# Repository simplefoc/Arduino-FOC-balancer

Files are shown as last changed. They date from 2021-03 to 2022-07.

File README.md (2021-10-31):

# Arduino *Simple**FOC**Balancer*

Modular Arduino two wheel balancing robot based on gimbal BLDC motors and *Simple**FOC**library*.
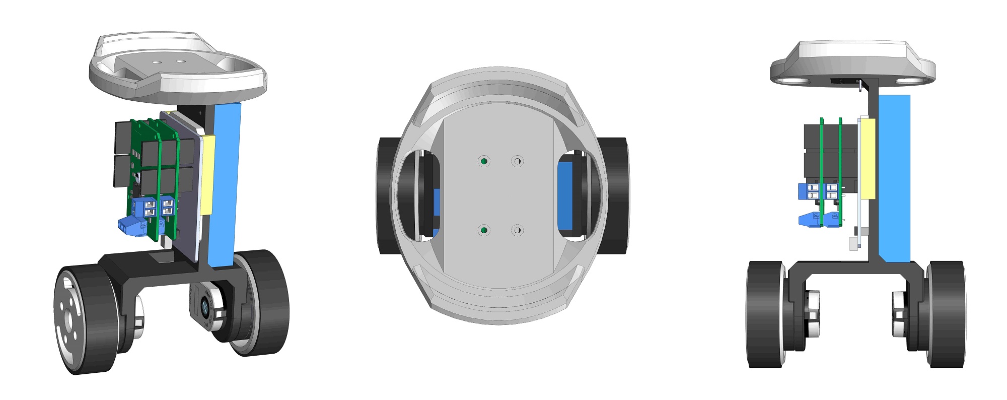
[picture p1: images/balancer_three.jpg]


Balancing robots are always a bit tricky to design, in order to make the robot balance we need to design and tune our mechanical structure and the control algorithm and, in the same time, choose optimal motors, sensors and microcontrollers. Therefore, even though BLDC motors are a great choice for balancing robots the complexity of their control made them undesirable. So this robot is an attempt to create a simple and modular, BLDC motor based, balancing robot that can be easily adapted for different *motor+sensor+mcu+driver* combinations and to show off the power and the awesome dynamics of gimbal BLDC motors 😄

## YouTube video demo
<a href="https://www.youtube.com/watch?v=f9GJqqUpL2w">
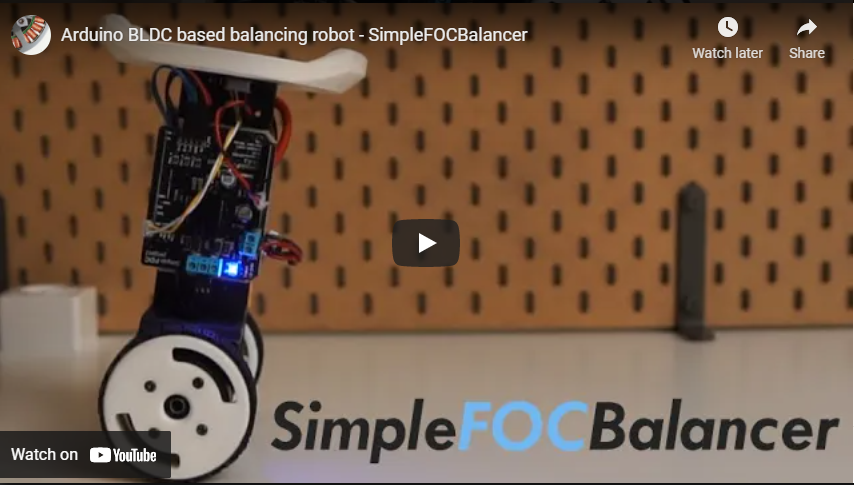
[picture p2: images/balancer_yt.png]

</a>

## Readme structure
- [Mechanical components](#mechanical-components)
    - [ 3D printed parts](#3d-printed-parts)
    - [Hardware parts](#hardware-parts)
- [Electrical components](#electrical-components)
    - [BLDC motor](#bldc-motor)
    - [Position sensors](#position-sensors)
    - [BLDC motor](#bldc-driver)
    - [IMU module](#imu-module)
    - [Bluetooth module](#bluetooth-module)
    - [Microcontroller](#microcontroller)
- [Arduino Code](#arduino-code)
    - [Control algorithm](#control-algorithm)
    - [Bluetooth remote control](#bluetooth-remote-control)

## Mechanical components
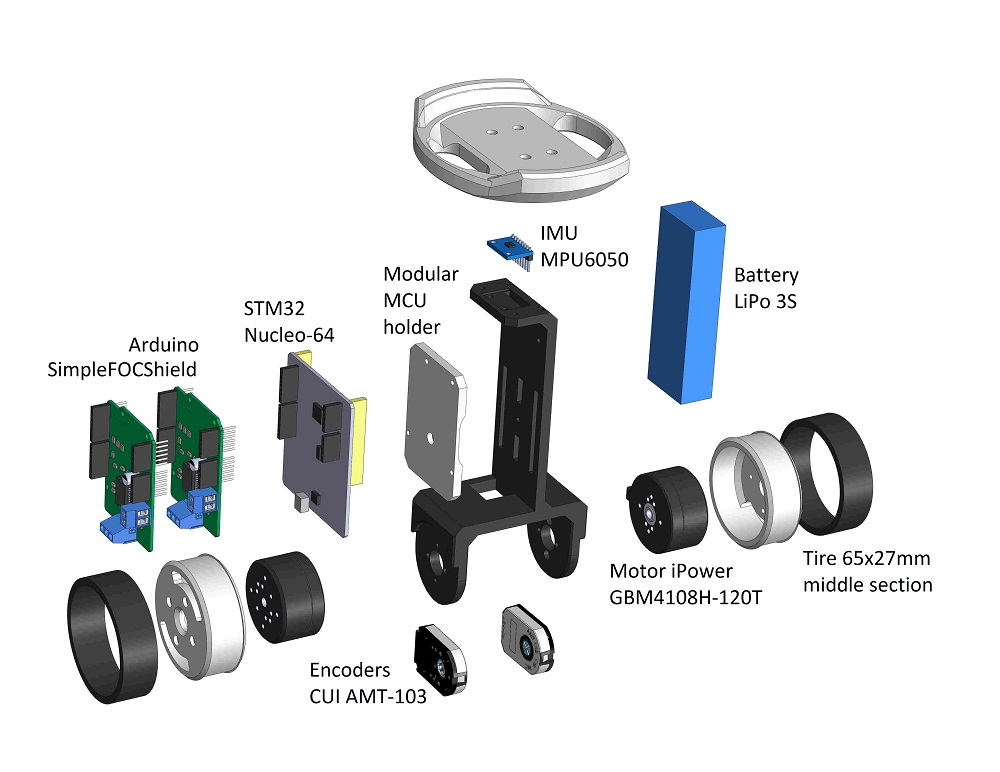
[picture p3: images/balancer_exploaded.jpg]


### 3D printed parts
This balancer project has 5 3d printed parts. You can find them in the `CAD > STL` directory. They are:
- center frame (`FOC_balancer.stl`)
    - infill: `30%`
    - layer hight: `>0.15mm`
- wheels (`wheel.stl`) 
    - infill: `30%`
    - layer hight: `0.1-0.15mm`
    - ***reasonably precise***
- MCU mount (`arduino_holder.stl`)
    - infill: `30%`
    - layer hight: `>0.15mm`
- top plate (`top_plate.stl`)
    - infill: `20%`
    - layer hight: `>0.15mm`

I have printed the pendulum in the PLA filament but there should be no real difference in using PETG or ABS filaments, this is just what I had in hand at the moment.

You will also find all the CAD files used in this project in the `CAD` folder. I have included the Solidworks 2016 parts and the full assembly. Additionally all the parts are exported to STEP format for easier porting to the other CAD IDEs.

> Beware: 
I have designed the holes on the pendulum arm and the wheel to match perfectly the motor the encoders I was using, so please check the dimensions of your motors and encoder holes before printing 😄
***If you would prefer some other CAD format, let me know, maybe I can export it differently.***

### Hardware parts

The mechanical components you will need are two sets of screws which you can easily find in your hardware store and the RC car tires that can be bought in bulk online. 

Component | Description | Link | Price
---- | ---- | ---- | ----
 |M3 screws<br> 25pcs <br> M3x10mm | [Ebay](https://www.ebay.com/itm/M2-M2-5-M3-M4-M5-M6-M8-Stainless-Steel-Metric-Hex-Socket-Head-Cap-Screws-Bolt/123439613021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) | 2$
 | M4 screws & nuts<br> 2pcs <br> M4x50mm | [Ebay](https://www.ebay.com/itm/M2-M2-5-M3-M4-M5-M6-M8-Stainless-Steel-Metric-Hex-Socket-Head-Cap-Screws-Bolt/123439613021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) | 4$
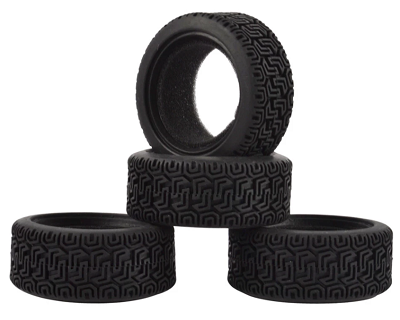
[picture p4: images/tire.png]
 |RC wheel <br>HSP HPI 8014 <br>2pcs <br> 69.5mmx29mm | [Aliexpress](https://www.aliexpress.com/item/32947563689.html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,searchweb201602_,searchweb201603_) | 5$

## Electrical components
### BLDC motor
The BLDC motors I was using in my video are an old versions of the [iPower GM4108](https://shop.iflight-rc.com/index.php?route=product/product&product_id=217&search=GM4108H-120T) motors which are not available anymore, in any case I was not able to find a website that would sell them. 
The good news is that you can use basically any other gimbal motor in that class with only minor modifications, mostly in the CAD parts - change the mounting holes positions. Some of the motors I was able to find that would be the most similar to my motor would be:

Component | Description | Link | Price
---- | ---- | ---- | ----
 | iPower Motor GM4108H-120T | [iFlight webshop](https://shop.iflight-rc.com/index.php?route=product/product&product_id=217&search=GM4108H-120T) | 35$
 | BGM4108-150HS | [Ebay](https://www.ebay.com/itm/New-Brushless-Gimbal-Motor-BGM4108-150HS-24N22P-for-Sony-NEX5-7-Camera-Mount-DIY/261903969970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) | 32$

### Position sensors
In my case I was using two encoders for the two motors. Now, this is very specific to my particular implementation, with minor CAD modifications you can use any type of the position sensor that is supported by the *Simple**FOC**library*. [Click here](https://docs.simplefoc.com/position_sensors) to see the documentation of the supported sensors. 

The encoders I have used in this project are:

 | AMT103 CUI | [Mouser](https://eu.mouser.com/ProductDetail/CUI-Devices/AMT103-V?qs=WyjlAZoYn51X2GCrrvGQTg==T) | 20$
---- | ---- | ---- | ----

### BLDC driver
In this project I used the [*Simple**FOC**Shield* v2.0.3](https://docs.simplefoc.com/arduino_simplefoc_shield_showcase) which is basically an Arduino shield which enables the usage of the FOC algorithm with the BLDC motors. It is practically plug & play in combination with the Arduino [*Simple**FOC**library*](https://docs.simplefoc.com/arduino_simplefoc_library_showcase).

But there is a lot of different boards that you can use to make this balancer. Basically any gimbal motor driver that is supported by the *Simple**FOC**library* will be suitable.  [Click here](https://docs.simplefoc.com/bldc_drivers) to see the documentation of the supported drivers. Here are some examples of the possible BLDC drives you could use:

Examples | Description | Link | Price
---- | ---- | ---- | ---
[](https://simplefoc.github.io/simplefoc_shield_product)| *Simple**FOC**Shield* v1/v2 | [More info](https://simplefoc.github.io/simplefoc_shield_product) | 20$
[](https://www.ebay.com/itm/BGC-3-1-MOS-Large-Current-Two-Axis-Brushless-Gimbal-Controller-Driver-Alexmos/302692769869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)| BGC 3.1 | [More info](https://www.ebay.com/itm/BGC-3-1-MOS-Large-Current-Two-Axis-Brushless-Gimbal-Controller-Driver-Alexmos/302692769869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) | 10$
[](https://www.ebay.com/itm/Storm32-BGC-32Bit-3-Axis-Brushless-Gimbal-Controller-V1-32-DRV8313-Motor-Driver/174343022855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) | Storm32 BGC | [Ebay](https://www.ebay.com/itm/Storm32-BGC-32Bit-3-Axis-Brushless-Gimbal-Controller-V1-32-DRV8313-Motor-Driver/174343022855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) | 25$

## IMU module

I've used the IMU MPU6050 with integrated DMP. It is a great board, very cheap and very powerful. You can use any other accelerometer to make the balancing robot but you might need to do some coda adaptation, mostly in the `imu_helpers.cpp/h`.

Examples | Description | Link | Price
---- | ---- | ---- | ---
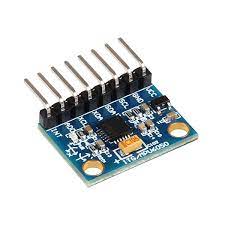
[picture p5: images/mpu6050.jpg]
[](https://www.amazon.fr/ARCELI-MPU6050-Acc%C3%A9l%C3%A9rom%C3%A8tre-Gyroscope-Convertisseur/dp/B07BVXN2GP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)| MPU6050  | [Amazon](https://www.amazon.fr/ARCELI-MPU6050-Acc%C3%A9l%C3%A9rom%C3%A8tre-Gyroscope-Convertisseur/dp/B07BVXN2GP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) | 2-5$

## Bluetooth module

If using the `ESP32` based mcu you will not need an additional Bluetooth module. But if you decide to go with some other mcu, I advise you to use the `HC-05`/`HC-06` modules, they are very simple to use and will work out of the box with the code.

Examples | Description | Link | Price
---- | ---- | ---- | ---
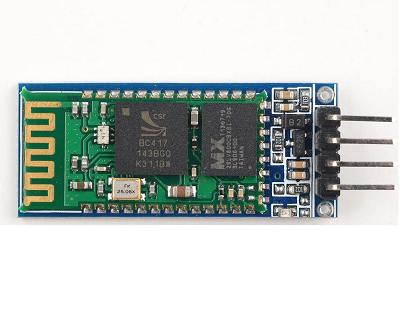
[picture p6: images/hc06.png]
[](https://www.amazon.fr/SunFounder-Wireless-Bluetooth-Transceiver-Backplane/dp/B00GAXG9A6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)| HC-06  | [Amazon](https://www.amazon.fr/SunFounder-Wireless-Bluetooth-Transceiver-Backplane/dp/B00GAXG9A6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) | 2-10$

## Microcontroller

In my example I've used EPS32 based microcontroller and the Stm32 based one but any type of the MCU that is supported by the *Simple**FOC**library* will do. [Click here](https://docs.simplefoc.com/microcontrollers) to see the documentation of the supported microcontrollers. 

Examples | Description | Link | Price
---- | ---- | ---- | ---
[](https://simplefoc.github.io/simplefoc_shield_product)| WeMos D1 R32  | [More info](https://www.amazon.com/Arduino-Wireless-Bluetooth-Development-Memory/dp/B07W1K56LN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) | 10$
[](https://www.mouser.fr/ProductDetail/STMicroelectronics/NUCLEO-F446RE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)| Nucleo-64 F411RE | [More info](https://www.mouser.fr/ProductDetail/STMicroelectronics/NUCLEO-F446RE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) | 15$

If using the gimbal controller boards such as BGC3.0/BGC3.1, Storm32 or similar you will do not bea able to change your microcontroller because it is integrated into the boards.

## Arduino code

still not complete

### Control algorithm
The control algorithm implemented in the Arduino sketch is very simple. It is a 2 PID controller cascade shown on the image bellow. 

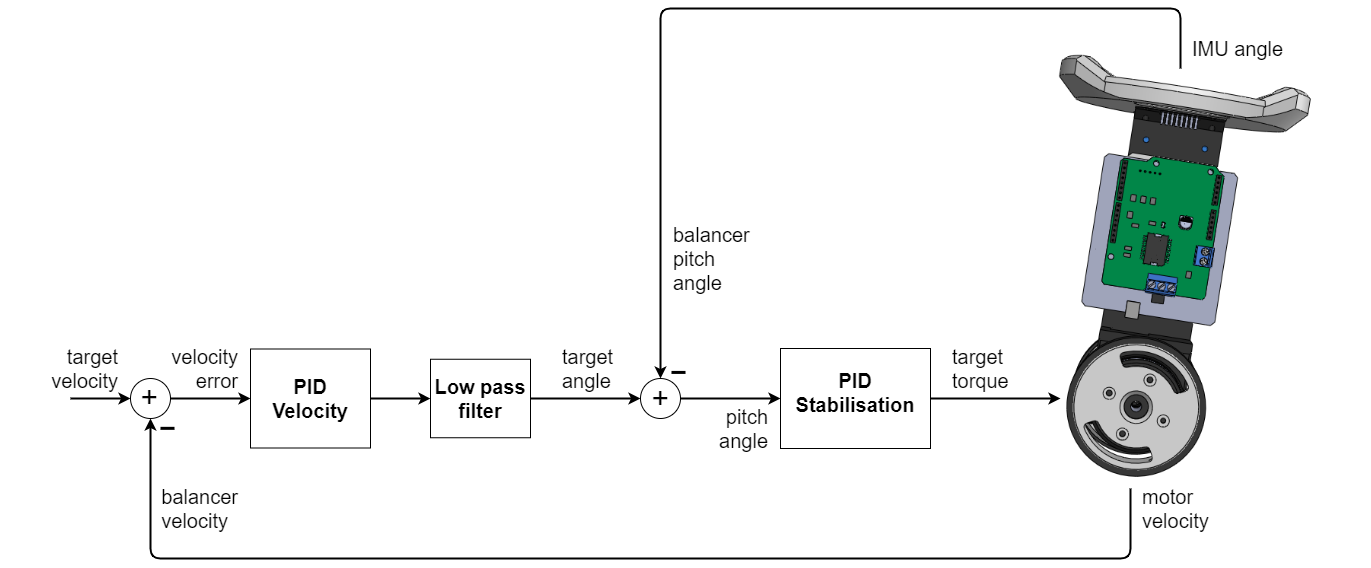
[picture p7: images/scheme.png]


The PID stabilisation controller will make sure that any target angle that is defined by the PID velocity is reached as soon as possible. Where PID velocity will try to keep the balancer robot moving with desired velocity defined by the user. This simple scheme is very powerful because it will make the balancer stand still even if the balancer zero angle has some offset. 

Here is the arduino code of the controller:
```cpp
// read pitch from the IMU
float pitch = getPitchIMU();
// calculate the target angle for throttle control
float target_pitch = lpf_pitch_cmd(pid_vel((motor1.shaft_velocity + motor2.shaft_velocity) / 2 - lpf_throttle(throttle)));
// calculate the target voltage
float voltage_control = pid_stb(target_pitch - pitch);

// filter steering
float steering_adj = lpf_steering(steering);
// set the tergat voltage value
motor1.target = voltage_control + steering_adj;
motor2.target = voltage_control - steering_adj;
```
The balancer velocity is estimated as average velocity for each wheel separately `(motor1.shaft_velocity + motor2.shaft_velocity) / 2`.  The target velocity is defined by the `throttle` variable set by the user. In addition to the `throttle` user can set the `steering` variable which will determine turning rate of the robot. The units of the `steering` variable are Volts in the provided example.

The PID parameters and filtering values can be changed by changing the definition of the `pid_stb` and `pid_vel`:
```cpp
// control algorithm parameters
// stabilisation pid
PIDController pid_stb{.P = 30, .I = 100, .D = 1, .ramp = 100000, .limit = 7};
// velocity pid
PIDController pid_vel{.P = 0.01, .I = 0.03, .D = 0, .ramp = 10000, .limit = _PI / 10};
// velocity control filtering
LowPassFilter lpf_pitch_cmd{.Tf = 0.07};
// low pass filters for user commands - throttle and steering
LowPassFilter lpf_throttle{.Tf = 0.5};
LowPassFilter lpf_steering{.Tf = 0.1};
```

### Bluetooth remote control

For remote controlling your robot you can use any wireless communication you wish. In my case I've used bluetooth with mobile joystick app. There is really a lot of them and you can choose the one that you prefer. In my case I've used an app called Gibalo. [Link to the google play app](https://play.google.com/store/apps/details?id=hr.fer.android.as46486.gibalo&hl=en&gl=US)

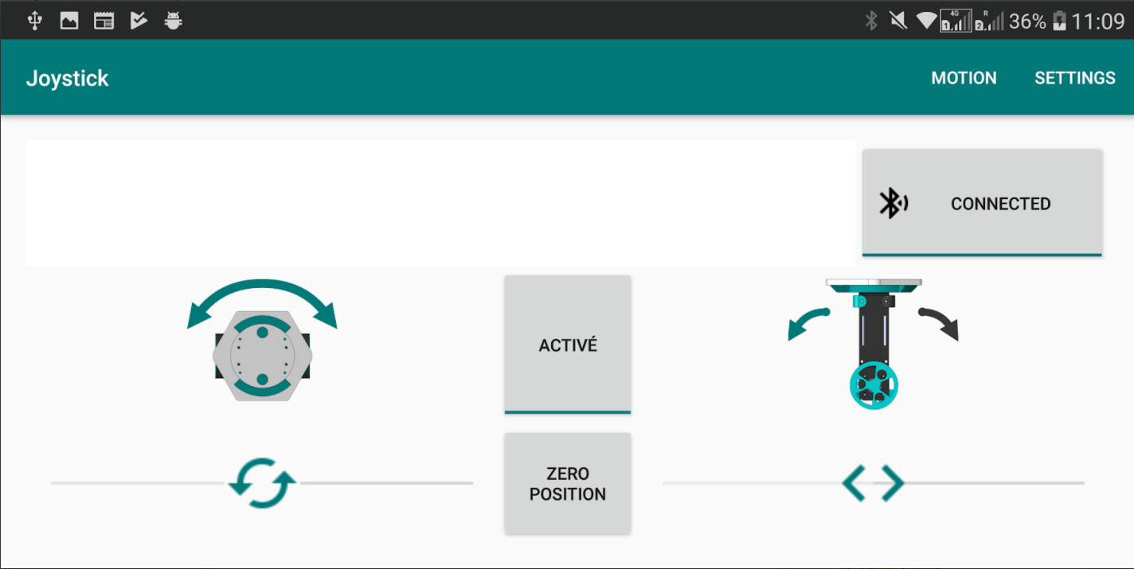
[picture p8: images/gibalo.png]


Regardless of the communication protocol that you choose to use the only three variables that you need to change in the balancer code are 
- `throttle` - target velocity of the balancer: value [-`max_throttle`, `max_throttle`] 
- `steering` - turning rate command: value [-`max_steering`, `max_steering`]
- `state` - `1` on,  `0` off

For the Gibalo app the Arduino code will be:
```cpp
/**
  Function intended for connecting to the Gibalo application
  In one byte it receives either throttle or steering command
  - if received byte  in range [0,200] then throttle command in between [-100, 100]
  - if received byte  in range [210,250] then steering command in between [-20, 20]
*/
void handleBluetooth(Stream& bt_port) {
  int inByte;
  if (bt_port.available() > 0) {
    while (bt_port.available()) {
      inByte = bt_port.read();
    }
    inByte = inByte - 100;
    if (inByte == 155) {
      // ON Byte
      steering = 0;
      throttle = 0;
      state = 1;
      bt_port.println("State ON");
    } else if (inByte == 154) {
      // OFF Byte
      steering = 0;
      throttle = 0;
      state = 0;
      bt_port.println("State OFF");
    } else if (inByte >= -100 && inByte <= 100) {
      // throttle set-point Byte
      throttle = max_throttle *  ((float)inByte) / 100.0;
    } else if (inByte >= 110 && inByte <= 150) {
      // steering set-point Byte
      steering = max_steering * ((float)(inByte - 130.0)) / 20.0;
    } else {
      // Error Byte
      steering = 0;
      throttle = 0;
      bt_port.println("Error number!");
    }
    bt_port.flush();
  }
}
```

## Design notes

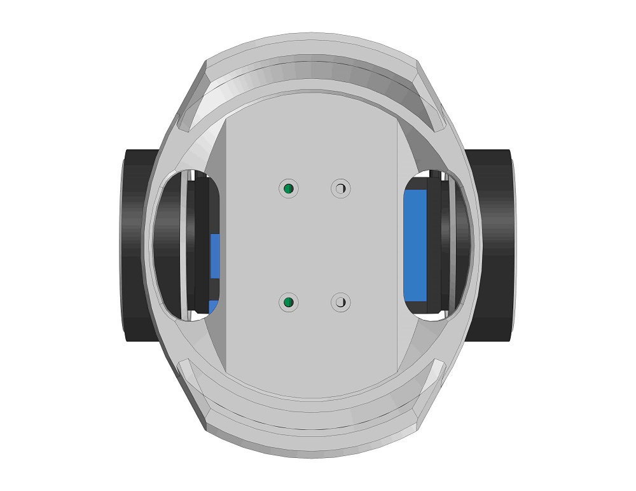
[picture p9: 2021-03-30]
images/balancer_t.JPG

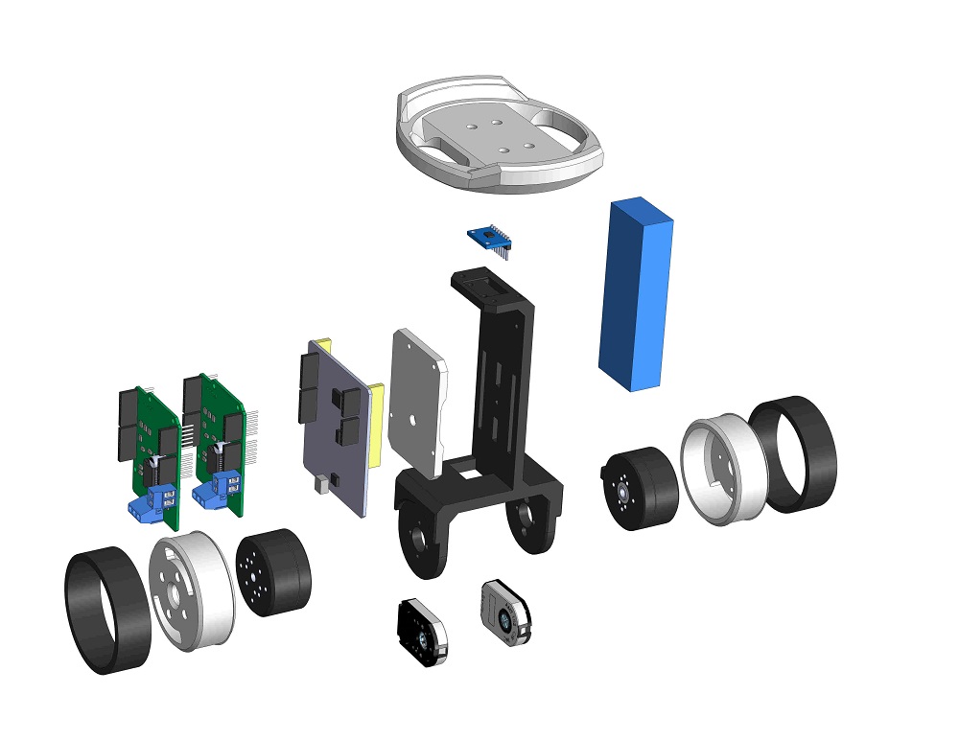
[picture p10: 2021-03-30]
images/balancer.JPG

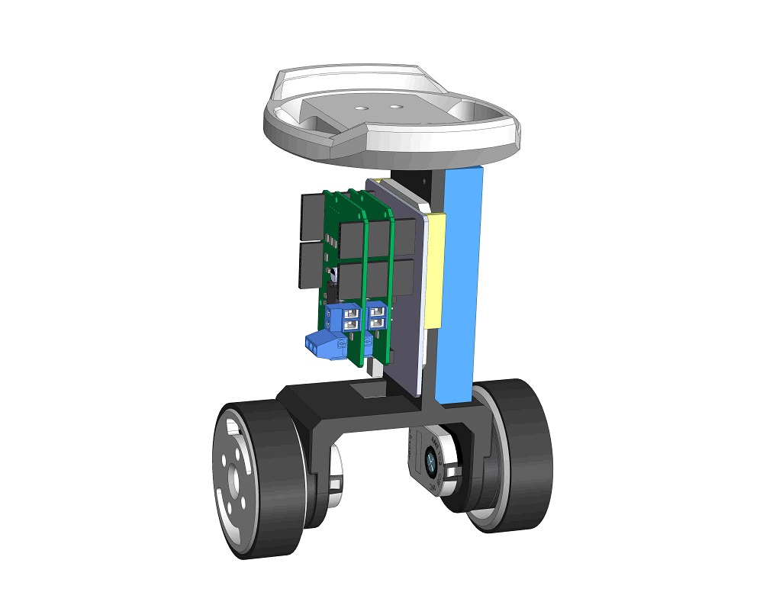
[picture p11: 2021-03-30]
images/balancer_s.JPG

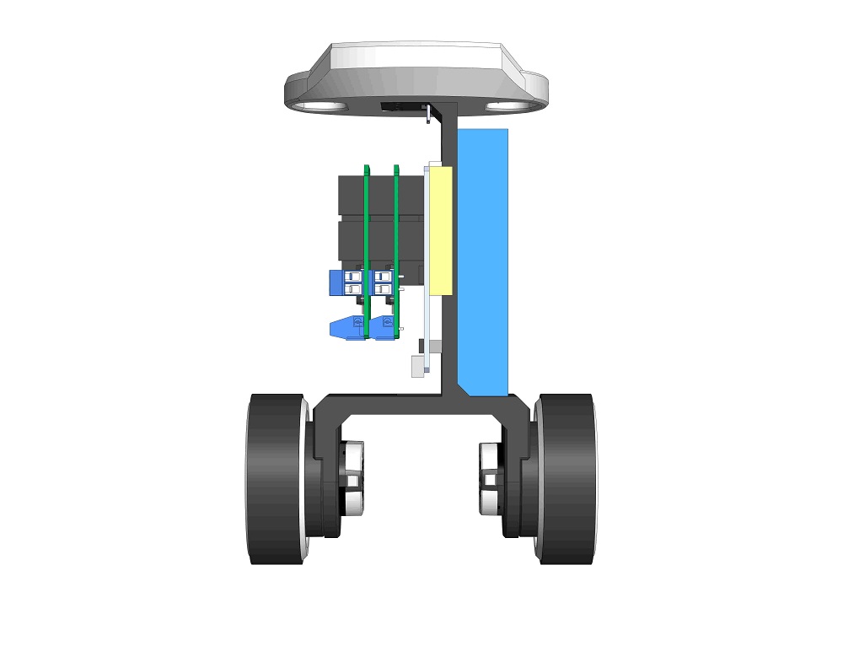
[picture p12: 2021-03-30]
images/balancer_front.JPG

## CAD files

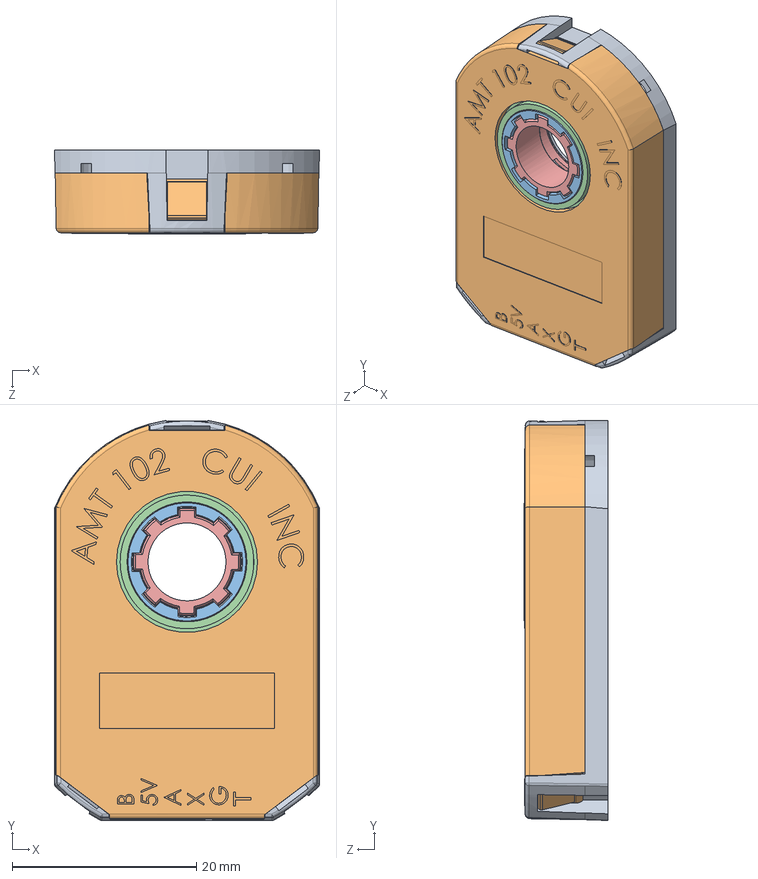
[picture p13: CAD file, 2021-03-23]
CAD/SolidWorks/AMT102/CUI_cui_amt102-0048-n2000-s.sldasm
28.8 x 43.4 x 9.15 mm
CUI_amt-102-base-rev-k
CUI_amt-102-top-cover-rev-h
CUI_amt-hub-top-rev-d1
CUI_amt-hub-bottom-rev-b
CUI_amt10x-shaft-adaptor-rev-e

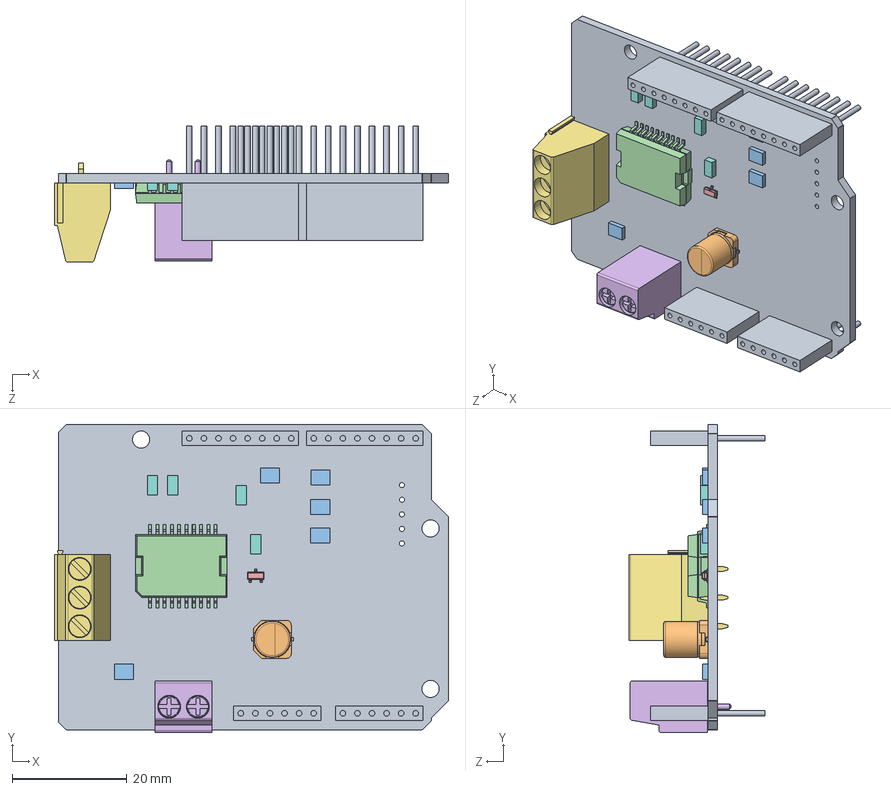
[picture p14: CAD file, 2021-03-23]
CAD/SolidWorks/SimpleFOCShield/ArduinoFOC.SLDASM
68.7 x 53.7 x 23.8 mm
Board
User_Library-A3D-003-00012
Extruded x 5
L6234PD x 2
User_Library-BAT54 x 2
2_RGB15238730
37753_RGB15238730
Extruded_2 x 4
headers

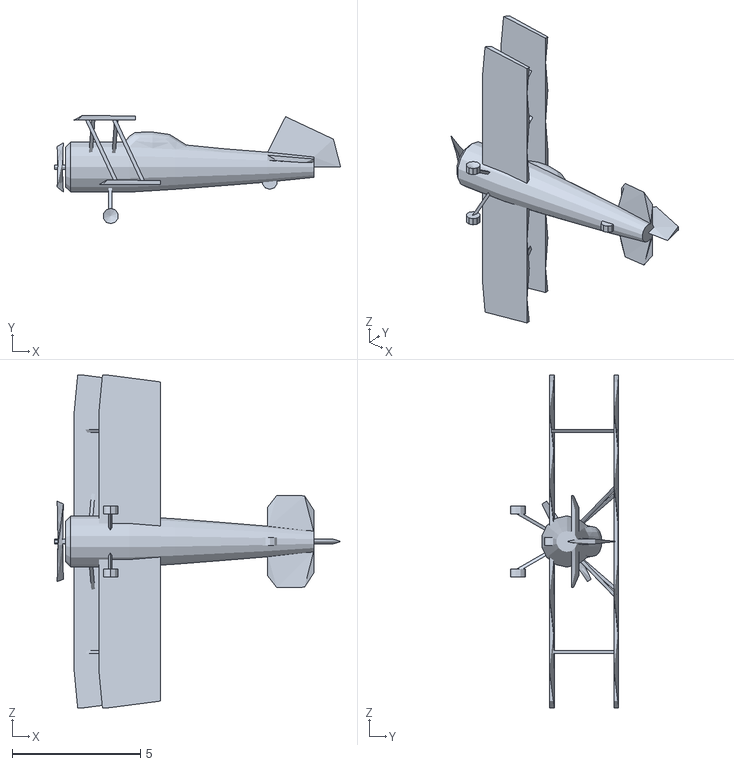
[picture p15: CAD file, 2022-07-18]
Arduino/simplefoc_balancer/src/MPU6050/Examples/MPU6050_DMP6_using_DMP_V6.12/MPUplane/data/biplane.obj
11.2 x 4.23 x 13.0

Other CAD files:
CAD/SolidWorks/SimpleFOCShield/PULL_B.sldasm
CAD/SolidWorks/SimpleFOCShield/C1.sldasm
CAD/SolidWorks/SimpleFOCShield/C2.sldasm
CAD/SolidWorks/SimpleFOCShield/R2.sldasm
CAD/SolidWorks/SimpleFOCShield/BAT1.sldasm
CAD/SolidWorks/SimpleFOCShield/PULL_A.sldasm
CAD/SolidWorks/SimpleFOCShield/C4.sldasm
CAD/SolidWorks/SimpleFOCShield/PULL_I.sldasm
CAD/SolidWorks/SimpleFOCShield/C3.sldasm
CAD/SolidWorks/SimpleFOCShield/L6234.sldasm
CAD/SolidWorks/SimpleFOCShield/TB_PWR.sldasm
CAD/SolidWorks/SimpleFOCShield/TB_M1.sldasm
CAD/SolidWorks/SimpleFOCShield/CAP1.sldasm
CAD/SolidWorks/SimpleFOCShield/R1.sldasm
CAD/SolidWorks/AMT102/CUI_amt10x-shaft-adaptor-rev-e.sldprt
CAD/STL/FOC_balancer.STL
CAD/STL/arduino_holder.STL
CAD/STL/top_plate.STL
CAD/STL/wheel.STL
CAD/SolidWorks/AMT102/CUI_amt-102-base-rev-k.sldprt
CAD/SolidWorks/AMT102/CUI_amt-102-top-cover-rev-h.sldprt
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

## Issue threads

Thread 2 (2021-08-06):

Adding current sensing for each motor with Wemos D1 R32

RoboKez, 2021-08-06:
This is a great project! I have successfully replicated it with the same hardware (except I used magnetic encoders). I'm now looking to add current sensing.

I have the same 2.0.3 shield pinout configuration you used and the same Wemos D1 R32. However A1 and A2 are not defined for the wemos D1 R32 when the board is set to the "WEMOS D1 MINI ESP32" in the Arduino IDE. Do you know what pins I should define as A1 and A2?

Thanks again

Kez

askuric, 2021-08-07:
Hey @RoboKez,
I'm happy to hear that!
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

As far as I know, none of the Arduino analog pins should be defined for the esp32 boards.

The pinout is in most cases printed on the board weemos board, you can verify if it is the same on the image.
If it is your analog pons should be:
- `A0` - 2
- `A1` - 4
- `A2` - 35
- `A3` - 34
I hope it helps 🙂

RoboKez, 2021-08-09:
Great thanks @askuric! Do I want to include **current_sense.gain_b *=-1;** for the v2.0.3 sheild? Also I noticed you set the voltage power supply to 12v in the video but change it to 8v on github. Should it be 8 as the 8v regulator is enabled?

askuric, 2021-08-09:
Hey Kez,
The `current_sense.gain_b =-1;` you can includebut you do not have to, since the `initFOC` will do the current sensor alignment itself and it should find this automatically.
But since you know this beforehand you can avoid current sense alignment by setting the:
```cpp
....
current_sense.gain_b =-1;
// skip alignment procedure
current_sense.skip_align = true;
motor.initFOC()
```

In the git code I've set it the power supply to 8V only because I've used 2 cell battery latter on; instead of 3cell one as in the video.
8V regulator does not have anything to do with this, 8V go only to the VIN port of the microcontroller and the full power supply voltage is powering the motor.

RoboKez, 2021-08-11:
Great, that makes sense. Thanks again @askuric! 👍

Closed 2021-08-11.

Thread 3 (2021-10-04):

pid tuning approach

RoboKez, 2021-10-04:
Hi @askuric!

This is a great stable system, what approach did you take to tuning the gains? Also on a separate note their is a minor capital error in line 9 of the balancer_pinouts.h,  MOT1_En should be MOT1_EN

Thanks again,

Kez

askuric, 2021-10-31:
Hey @RoboKez !
Thanks for the message and I am sorry that I did not respond earlier.
I've updated the typo in the variable naming of the motor 1 enable pin.

Regarding the tuning procedure, it is a really good question. I've somewhat hinted it once in the community post about this robot, I hope you'll find it useful. 😄
https://community.simplefoc.com/t/self-balancing-robot/343/24?u=antun_skuric

But basically, I was not trying to model this robot at all, all the PIDs are hand-tuned using the described procedure. The model of the robot would not be that much more difficult to find, since the cad model is pretty precise and all the masses of the components can be measured pretty well. And you could even approximate the BLDC motor with the DC motor dynamics. And once you have your dynamical system you can find an optimal PID stabilization controller based on different stability criteria as Hurwitz or similar. But I did not go there for this project. 😄

For the motion control it becomes a bit more complicated, since you need to control the balancer angle to produce the desired movement and to stay stable. And as the motion control (velocity control) cannot be separated from the stabilization control then there are no really simple control engineering procedures to solve this. So the easiest way is to hand tune it, because the dynamics of these BLDC motors are awesome and even with suboptimal PID parameters the segway is very dynamic and stable. 😄

I hope it helps, I am not sure if I've answered your question though. 😄

RoboKez, 2022-03-26:
Hi @askuric ,

Thanks for the response and the post was very helpful! I'm really enjoying th SimpleFOC library awesome work!

Cheers,
Kez

Closed 2022-03-26.

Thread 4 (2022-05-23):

Doesn't work with ESP32

yufuping, 2022-05-23:
MPU6050 dies at initialize()

Environment:
1. ESP32 Ver2.03

askuric, 2022-07-18:
Hey @yufuping,

Youre right with the newer version of the Espressif framework the i2cdev library stopped working : https://github.com/jrowberg/i2cdevlib/issues/688

I've updated the i2c dev library in this repo and implemented the propsed fix. The code now works again 😄

Closed 2022-10-03.

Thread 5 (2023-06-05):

Pinout for IMU?

PatchBOTS, 2023-06-05:
Hi,
  I can't seem to find the pin numbers for the IMU to the Nucleo/Arduino.

adornelas, 2024-01-25:
Hello, @PatchBOTS
Not a contributer here but I believe there are no pinouts for the IMU because it communicates through I2C pins, so in Arduino those would be SDA and SCL pins.

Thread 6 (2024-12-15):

Redesign of the 3d printer main frame + find solution to connect encoder properly

Klipton1, 2024-12-15:
When ordering motors for this project, i.e., 2x GBM5108-120T you find out that the hole pattern is different and that there is now a hollow shaft. How would one change the mechanical design to connect the encoders?

I made an error in the mechanical design as I was currently putting a clamping force on the hollow shaft. This in turn lead to motor problems running not smooth anymore. Any help, tips or tricks would be greatly appreciated!

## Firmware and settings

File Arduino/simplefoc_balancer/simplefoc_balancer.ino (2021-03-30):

#include <SimpleFOC.h>

#include "balancer_pinouts.h"
#include "imu_helpers.h"

// serial instance for bluetooth communication
// ESP32 bluetooth serial
#include "BluetoothSerial.h"
BluetoothSerial bluetooth;
// bluetooth nucleo stm32
// HardwareSerial bluetooth(PA12, PA11);

// create motor and driver instances
BLDCMotor motor1 = BLDCMotor(11);
BLDCMotor motor2 = BLDCMotor(11);
BLDCDriver3PWM driver1 = BLDCDriver3PWM(MOT1_A, MOT1_B, MOT1_C, MOT1_EN);
BLDCDriver3PWM driver2 = BLDCDriver3PWM(MOT2_A, MOT2_B, MOT2_C, MOT2_EN);

// create the encoder instances
Encoder encoder1 = Encoder(ENC1_A, ENC1_B, 500);
// interrupt ruotine intialisation
void doA1() {  encoder1.handleA(); }
void doB1() {  encoder1.handleB(); }
Encoder encoder2 = Encoder(ENC2_A, ENC2_B, 500);
void doA2() {  encoder2.handleA(); }
void doB2() {  encoder2.handleB();}

// control algorithm parameters
// stabilisation pid
PIDController pid_stb{.P = 30, .I = 100, .D = 1, .ramp = 100000, .limit = 7};
// velocity pid
PIDController pid_vel{.P = 0.01, .I = 0.03, .D = 0, .ramp = 10000, .limit = _PI / 10};
// velocity control filtering
LowPassFilter lpf_pitch_cmd{.Tf = 0.07};
// low pass filters for user commands - throttle and steering
LowPassFilter lpf_throttle{.Tf = 0.5};
LowPassFilter lpf_steering{.Tf = 0.1};

// Bluetooth app variables
float steering = 0;
float throttle = 0;
float max_throttle = 20; // 20 rad/s
float max_steering = 1; // 1 V
int state = 1; // 1 on / 0 off

// motion control tunning using commander
Commander commander = Commander(Serial);
void cntStab(char* cmd) {  commander.pid(&pid_stb, cmd);}
void cntMove(char* cmd) {  commander.pid(&pid_vel, cmd);}
void lpfPitch(char* cmd) {  commander.lpf(&lpf_pitch_cmd, cmd);}
void lpfSteering(char* cmd) {  commander.lpf(&lpf_steering, cmd);}
void lpfThrottle(char* cmd) {  commander.lpf(&lpf_throttle, cmd);}

void setup() {
  // use monitoring with Serial for motor init
  // monitoring port
  Serial.begin(250000);
  // bluetooth esp32
  bluetooth.begin("FOCBalancer_esp");
  // bluetooth nucleo
  //  bluetooth.begin(115200);

  _delay(1000);
  // imu init and configure
  if ( !initIMU() ) {
    Serial.println(F("IMU connection problem... Disabling!"));
    bluetooth.println(F("IMU connection problem... Disabling!"));
    return;
  }
  _delay(1000);

  // initialise encoder hardware
  encoder1.init();
  encoder1.enableInterrupts(doA1, doB1);
  encoder2.init();
  encoder2.enableInterrupts(doA2, doB2);

  // link the motor to the sensor
  motor1.linkSensor(&encoder1);
  motor2.linkSensor(&encoder2);

  // power supply voltage [V]
  driver1.voltage_power_supply = 8;
  driver1.init();
  motor1.linkDriver(&driver1);
  driver2.voltage_power_supply = 8;
  driver2.init();
  motor2.linkDriver(&driver2);

  // set control loop type to be used
  // using voltage torque mode
  motor1.controller = MotionControlType::torque;
  motor2.controller = MotionControlType::torque;

  // enable monitoring
  motor1.useMonitoring(Serial);
  motor2.useMonitoring(Serial);

  // initialise motor
  motor1.init();
  motor2.init();
  // align encoder and start FOC
  motor1.initFOC();
  motor2.initFOC();

  // add the configuration commands
  commander.add('A', cntStab, "pid stab");
  commander.add('B', cntMove, "pid vel");
  commander.add('C', lpfThrottle, "lpf vel command");
  commander.add('D', lpfPitch, "lpf throttle");
  commander.add('E', lpfSteering, "lpf steering");

  Serial.println(F("Balancing robot ready!"));
  bluetooth.println(F("Balancing robot ready!"));
}


void loop() {
  // iterative setting FOC phase voltage
  motor1.loopFOC();
  motor2.loopFOC();

  // iterative function setting the outter loop target
  motor1.move();
  motor2.move();

  if (!state) { // if balancer disabled
    motor1.target = 0;
    motor2.target = 0;
  } else if ( hasDataIMU() ) { // when IMU has received the package
    // read pitch from the IMU
    float pitch = getPitchIMU();
    // calculate the target angle for throttle control
    float target_pitch = lpf_pitch_cmd(pid_vel((motor1.shaft_velocity + motor2.shaft_velocity) / 2 - lpf_throttle(throttle)));
    // calculate the target voltage
    float voltage_control = pid_stb(target_pitch - pitch);
    
    // filter steering
    float steering_adj = lpf_steering(steering);
    // set the tergat voltage value
    motor1.target = voltage_control + steering_adj;
    motor2.target = voltage_control - steering_adj;
  }

  // read the tuning commands from Serial
  commander.run();
  // read the user command from bluetooth
  handleBluetooth(bluetooth);
}

/**
  Function intended for connecting to the Gibalo application
  In one byte it receives either throttel or steering command
  - if received byte  in range [0,200] then throttle command in between [-100, 100]
  - if received byte  in range [210,250] then steering command in between [-20, 20]
*/
void handleBluetooth(Stream& bt_port) {
  int inByte;
  if (bt_port.available() > 0) {
    while (bt_port.available()) {
      inByte = bt_port.read();
    }
    inByte = inByte - 100;
    if (inByte == 155) {
      // ON Byte
      steering = 0;
      throttle = 0;
      state = 1;
      bt_port.println("State ON");
    } else if (inByte == 154) {
      // OFF Byte
      steering = 0;
      throttle = 0;
      state = 0;
      bt_port.println("State OFF");
    } else if (inByte >= -100 && inByte <= 100) {
      // throttle set-point Byte
      throttle = max_throttle *  ((float)inByte) / 100.0;
    } else if (inByte >= 110 && inByte <= 150) {
      // steering set-point Byte
      steering = max_steering * ((float)(inByte - 130.0)) / 20.0;
    } else {
      // Error Byte
      steering = 0;
      throttle = 0;
      bt_port.println("Error number!");
    }
    bt_port.flush();
  }
}

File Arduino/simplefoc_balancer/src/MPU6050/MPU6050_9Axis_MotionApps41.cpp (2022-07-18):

// I2Cdev library collection - MPU6050 I2C device class, 9-axis MotionApps 4.1 implementation
// Based on InvenSense MPU-6050 register map document rev. 2.0, 5/19/2011 (RM-MPU-6000A-00)
// 6/18/2012 by Jeff Rowberg <jeff@rowberg.net>
// Updates should (hopefully) always be available at https://github.com/jrowberg/i2cdevlib
//
// Changelog:
//  2021/09/27 - split implementations out of header files, finally

/* ============================================
I2Cdev device library code is placed under the MIT license
Copyright (c) 2021 Jeff Rowberg

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
THE SOFTWARE IS PROVIDED "AS IS", WITHOUT WARRANTY OF ANY KIND, EXPRESS OR
IMPLIED, INCLUDING BUT NOT LIMITED TO THE WARRANTIES OF MERCHANTABILITY,
FITNESS FOR A PARTICULAR PURPOSE AND NONINFRINGEMENT. IN NO EVENT SHALL THE
AUTHORS OR COPYRIGHT HOLDERS BE LIABLE FOR ANY CLAIM, DAMAGES OR OTHER
LIABILITY, WHETHER IN AN ACTION OF CONTRACT, TORT OR OTHERWISE, ARISING FROM,
OUT OF OR IN CONNECTION WITH THE SOFTWARE OR THE USE OR OTHER DEALINGS IN
THE SOFTWARE.
===============================================
*/

// MotionApps 4.1 DMP implementation, built using the MPU-9150 "MotionFit" board
#define MPU6050_INCLUDE_DMP_MOTIONAPPS41

#include "MPU6050_9Axis_MotionApps41.h"

// Tom Carpenter's conditional PROGMEM code
// http://forum.arduino.cc/index.php?topic=129407.0
#ifdef __AVR__
    #include <avr/pgmspace.h>
#elif defined(ESP32)
	#define CONFIG_DISABLE_HAL_LOCKS 1
    #include <pgmspace.h>
#else
    // Teensy 3.0 library conditional PROGMEM code from Paul Stoffregen
    #ifndef __PGMSPACE_H_
        #define __PGMSPACE_H_ 1
        #include <inttypes.h>

        #define PROGMEM
        #define PGM_P  const char *
        #define PSTR(str) (str)
        #define F(x) x

        typedef void prog_void;
        typedef char prog_char;
        //typedef unsigned char prog_uchar;
        typedef int8_t prog_int8_t;
        typedef uint8_t prog_uint8_t;
        typedef int16_t prog_int16_t;
        typedef uint16_t prog_uint16_t;
        typedef int32_t prog_int32_t;
        typedef uint32_t prog_uint32_t;
        
        #define strcpy_P(dest, src) strcpy((dest), (src))
        #define strcat_P(dest, src) strcat((dest), (src))
        #define strcmp_P(a, b) strcmp((a), (b))
        
        #define pgm_read_byte(addr) (*(const unsigned char *)(addr))
        #define pgm_read_word(addr) (*(const unsigned short *)(addr))
        #define pgm_read_dword(addr) (*(const unsigned long *)(addr))
        #define pgm_read_float(addr) (*(const float *)(addr))
        
        #define pgm_read_byte_near(addr) pgm_read_byte(addr)
        #define pgm_read_word_near(addr) pgm_read_word(addr)
        #define pgm_read_dword_near(addr) pgm_read_dword(addr)
        #define pgm_read_float_near(addr) pgm_read_float(addr)
        #define pgm_read_byte_far(addr) pgm_read_byte(addr)
        #define pgm_read_word_far(addr) pgm_read_word(addr)
        #define pgm_read_dword_far(addr) pgm_read_dword(addr)
        #define pgm_read_float_far(addr) pgm_read_float(addr)
    #endif
#endif

// NOTE! Enabling DEBUG adds about 3.3kB to the flash program size.
// Debug output is now working even on ATMega328P MCUs (e.g. Arduino Uno)
// after moving string constants to flash memory storage using the F()
// compiler macro (Arduino IDE 1.0+ required).

//#define DEBUG
#ifdef DEBUG
    #define DEBUG_PRINT(x) Serial.print(x)
    #define DEBUG_PRINTF(x, y) Serial.print(x, y)
    #define DEBUG_PRINTLN(x) Serial.println(x)
    #define DEBUG_PRINTLNF(x, y) Serial.println(x, y)
#else
    #define DEBUG_PRINT(x)
    #define DEBUG_PRINTF(x, y)
    #define DEBUG_PRINTLN(x)
    #define DEBUG_PRINTLNF(x, y)
#endif

#define MPU6050_DMP_CODE_SIZE       1962    // dmpMemory[]
#define MPU6050_DMP_CONFIG_SIZE     232     // dmpConfig[]
#define MPU6050_DMP_UPDATES_SIZE    140     // dmpUpdates[]

/* ================================================================================================ *
 | Default MotionApps v4.1 48-byte FIFO packet structure:                                           |
 |                                                                                                  |
 | [QUAT W][      ][QUAT X][      ][QUAT Y][      ][QUAT Z][      ][GYRO X][      ][GYRO Y][      ] |
 |   0   1   2   3   4   5   6   7   8   9  10  11  12  13  14  15  16  17  18  19  20  21  22  23  |
 |                                                                                                  |
 | [GYRO Z][      ][MAG X ][MAG Y ][MAG Z ][ACC X ][      ][ACC Y ][      ][ACC Z ][      ][      ] |
 |  24  25  26  27  28  29  30  31  32  33  34  35  36  37  38  39  40  41  42  43  44  45  46  47  |
 * ================================================================================================ */
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

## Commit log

2020-12-29 initial arduino code added
2020-12-31 cad files initial and readme a bit more info
    [CUI_amt-102-base-rev-k.sldprt, CUI_amt-102-top-cover-rev-h.sldprt, CUI_amt-hub-bottom-rev-b.sldprt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]
2021-03-23 new version images
    [2_RGB15238730.sldprt, 37753_RGB15238730.sldprt, 5920131968.sldasm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]
2021-03-30 FEAT added more docs
    [balancer.SLDASM]
2021-03-30 images bt + imu
2022-07-18 updated I2Cdev library version + fix for ESP32
    [biplane.obj]
